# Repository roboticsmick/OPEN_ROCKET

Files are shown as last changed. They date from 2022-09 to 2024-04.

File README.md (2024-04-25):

# OPEN LOW COST ROCKET

An open designed low cost rocket build using 3D printed parts and a laser cutter. Design uses a Von Karman Nose Cone profile (optimum nose cone profile for rockets). Nosecone has space for a small payload bay. All parts should be printables without supports on Launchpad printers. You need to use the large Lulzbot due to height of nosecone. 29mm motor mount. A spacer is required for 24mm motor. Have successfully launched rocket using a E24 and G78 motor. 

Note: PLA deforms if left in the sun or it gets hot. Make sure to keep the nosecone out of the sun for extended periods of time. If it is in the sun, make sure the end caps are in to help reinforce the nosecone to prevent it deforming. 

#### Build 1:


#### Build 2:


## Parts list:
### Hardware to purchase:
1. 1 x PPS Mailing Tube 60 x 600 mm (Officeworks)
2. 3 x 12mm M3 countersunk hex bolts
3. 1 x M3 eyebolt - 10-15mm threaded bolt length (if the bolt length is longer and you have an avionics payload, make sure the bolt doesn't interfere with the avionics mounting in the nosecone)
4. 6 x M3 nuts
5. 2 x rail buttons (AusRocketry sell for $5)
6. 1 x parachute
7. 1 x nomex chute protector or wadding
8. 1 x shock cord - 2-3m long
9. 1 x epoxy
10. 2 x Sandpaper - 100 and 400 grit

### 3D printed parts:
1. 2 x Laser cutter jigs (holds the body tube straight and allows accurate 120 degree rotation of the body tube in the laser cutter when cutting out the fin slots).
2. 1 x Motor retainer (print with the thread at the top)
3. 1 x Motor tube (print with the thread at the top)
4. 1 x Nosecone plate / bulkhead
5. 1 x Nosecone (250mm length based on maximum Z Axis height of 3D printer).

### Plywood (4mm plywood):
3. 1 x laser shield (slots into laser cutter jig slot to prevent laser cutter from burning the opposing side of body tube when cutting fin slots)
4. 1 x Upper centring ring
5. 1 x Lower centring ring
6. 3 x Fins

## Steps:
### Body tube fin slots
1. Insert the laser cutter jigs into each end of the body tube. 
Rest the jigs on a flat surface and rotate and jiggle the tube until both jigs are sitting flat on the surface. Make sure they are still inserted into the tube. Add some masking tape to lock this position in place.
2. The jig has 3 centre markers for marking 3 equidistant marks on the tube to align laser cutter. 
3. Mark the tube at the marker points, then use a right angle ruler to draw lines along motor tube.
4. Measure up 66mm along the line and mark this point. This is where you will align the laser cutter centre point.
5. Insert the laser cutter shield into the slot parallel with the laser cutter bed. Rotate this piece of plywood after each cut. 
6. Make sure the laser cutter bed is correctly positioned and square in the lasercutter. Sometimes people bump it and it is not square. Insert the tube into laser cutter, and make sure the jig is aligned squarley with the lasercutter in one corner. The legs of the jig are square so it can be aligned against the lasercutter bed. It is important you place it in a repeatable position in the laser cutter, so that after the first cut of the fin slot, you can remove the jig, rotate it 120 degrees, then place it back into the same position. 




6. Centre the laser cutter on the mark made at the 66mm point and load in the fin slot template. You can position the laser cutter pointer to be in the centre of the object to be cut.
7. Cut the fin slot.
8. Remove the laser cutter shield, and rotate it to a new position that is parrallel to the next fin slot to cut.
9. Rotate the body tube, and reposition in the same location.
10. Recentre the laser cutter and repeat cut. 
11. Do this until all three fins are cut, remembering to move the laser cutter shield each time to prevent the laser cutter damaging the opposing wall.

### Fins and motor:
1. Glue upper ring to top of motor tube. Make sure it dries on a flat surface. Make sure not to get glue on fin guide slots or the holes to tie the parachute chord. 
2. Tie the parachute chord through the two holes in upper centering ring using a fishing knot.
3. Add epoxy fillet to upper ring and to the parachute chord to ensure strong bond and secure the chord. You can use a little masking tape after epoxying to keep the cord in the correct position to dry.
4. Place lower ring on motor tube and screw on motor retainer.
5. Test fit fins to ensure they fit cleanly into fin slots. Sand if needed.
6. Test fit motor tube into rocket body, noting were upper ring sits in motor tube.
7. Add glue to rocket body tube where the upper ring will sit.
8. Slide in motor tube to where glue sits. Align motor tube to fin slots and let dry.
9. Remove motor retainer cap and lower centering ring.
10. Add glue to guide slots and glue in fins. Motor tube has fin guides that will ensure fins are relatively straight. Leave to dry properly.
11. For added strength, add internal fillets to fins against body tube and motor tube.
12. Glue in lower centreing ring.
13. Use masking tape on outer tube to mask off where the outer fillets for the fins will go.
14. Add epoxy fillets for the fins.  Do this in 3 goes to allow time for the epoxy to settle when drying, before rotating to the next fin.
15. Remove the tape before epoxy sets fully and smooth epoxy againt body tube to minimise sanding when dry (otherwise there will be a little step the height of the masking tape).
16. Let epoxy set for 24 hours.





### Launch lugs / Rail buttons:
1. Drill holes into tube for rail buttons (1 into lower centring ring and 1 at centre of pressure (just below where the parachute sits in body tube to prevent it catching when it ejects)
2. Rough up where the rail buttons will mount on the body tube with sandpaper to allow a better grip for the epoxy.
3. Add epoxy into rail button holes, then screw in rail buttons. Clean up any excess epoxy with tissue.
4. For upper rail button, add extra epoxy to inner tube to ensure a more secure bond and prevent the thread sticking out and snagging the parachute (use a long piece of wood to get the epoxy into the tube and smooth it out so it creates a smooth blob around thread).

### Nosecone:
1. Clean out the nut mount inserts in the bulkhead to ensure there is no 3D filament stuck in the holes
2. Test fit the nuts to make sure they fit into points
3. Add small amount of epoxy to each of the nut mounts then press in the nuts (make sure no epoxy gets in the nut thread). You can use a nylon bolt to hold make sure the nuts are in place and no epoxy gets in the thread (just make sure to remove the bolt before the epoxy sets)
4. Screw in the eyebolt (add a little bit of epoxy when screwed in to prevent it from unwinding).
5. Attached shock cord and parachute to eyebolt.

#### Von Karman Nose Cone:


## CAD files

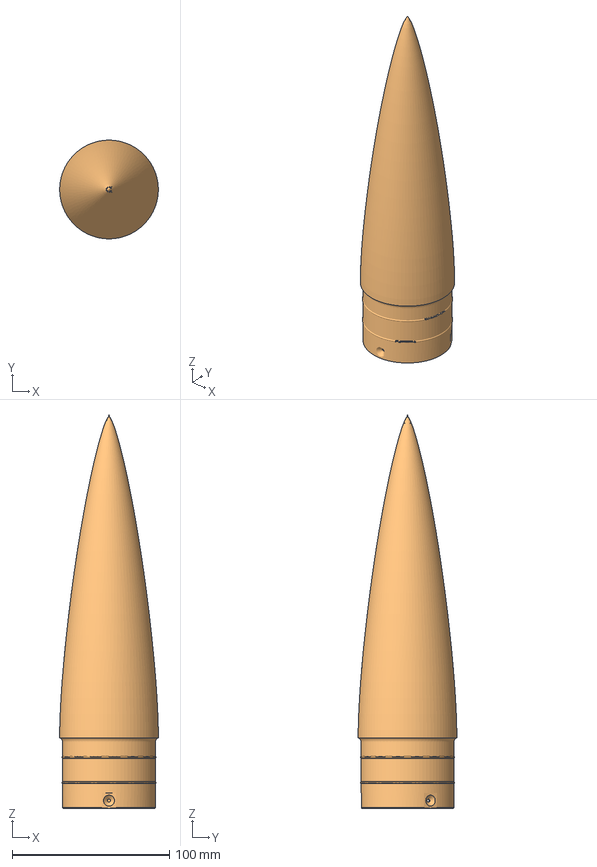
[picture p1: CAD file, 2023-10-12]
NOSECONE_VON_KARMAN.3mf
62.8 x 62.7 x 250.0 mm
Nose_Cone

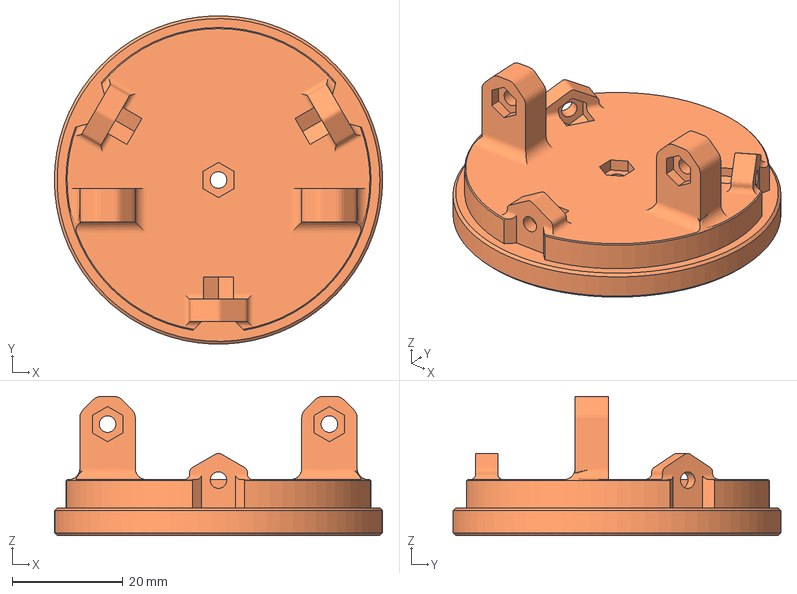
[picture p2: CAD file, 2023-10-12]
NOSECONE_PLATE.3mf
59.2 x 59.1 x 25.1 mm

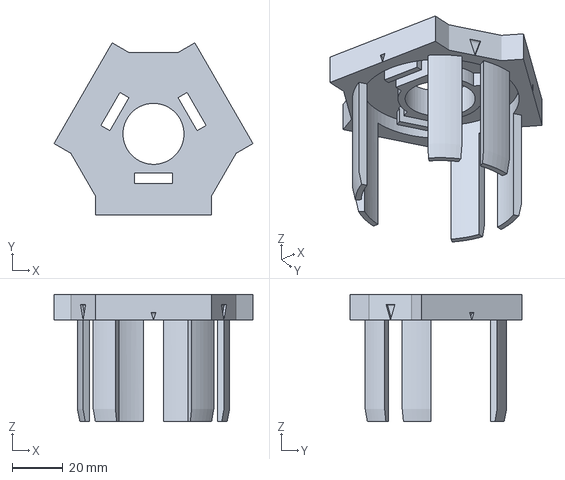
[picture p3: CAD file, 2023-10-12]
LASER_CUTTER_JIG.3mf
78.3 x 67.8 x 50.0 mm

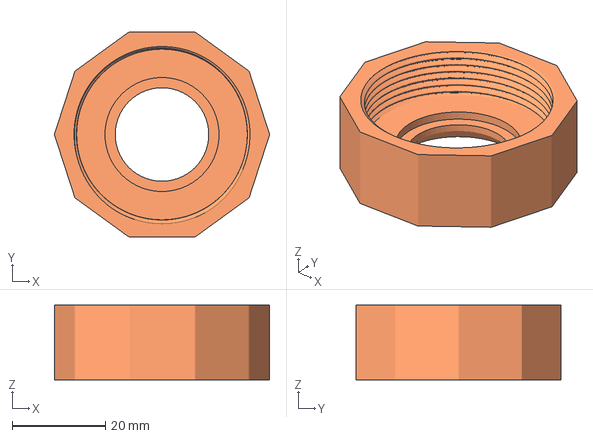
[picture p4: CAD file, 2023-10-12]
MOTOR_RETAINER.3mf
46.0 x 43.8 x 16.0 mm

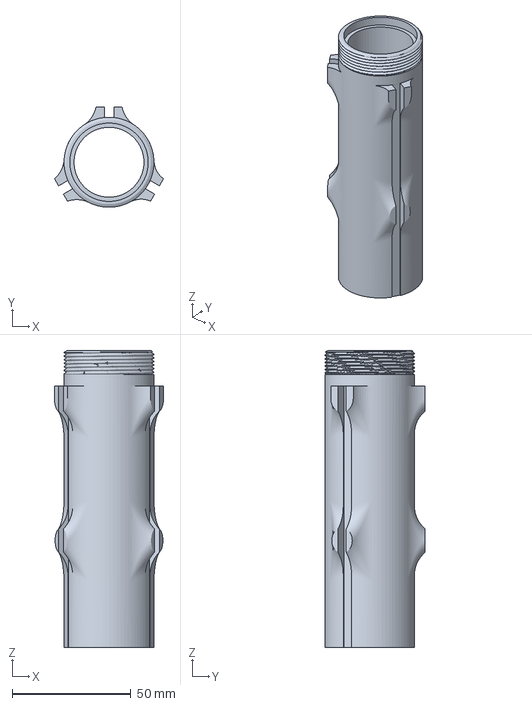
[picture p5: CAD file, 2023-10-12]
MOTOR_MOUNT.3mf
45.9 x 42.3 x 125.0 mm

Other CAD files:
FIN_BUILD_1.f3d
FIN_BUILD_2.f3d
LASER_CUTTER_JIG v8.f3d
MOTOR_RETAINER.f3d
NOSECONE_PLATE.f3d
NOSECONE_VON_KARMAN_FUSION360.f3d
SPACER_LOWER.f3d
SPACER_UPPER.f3d

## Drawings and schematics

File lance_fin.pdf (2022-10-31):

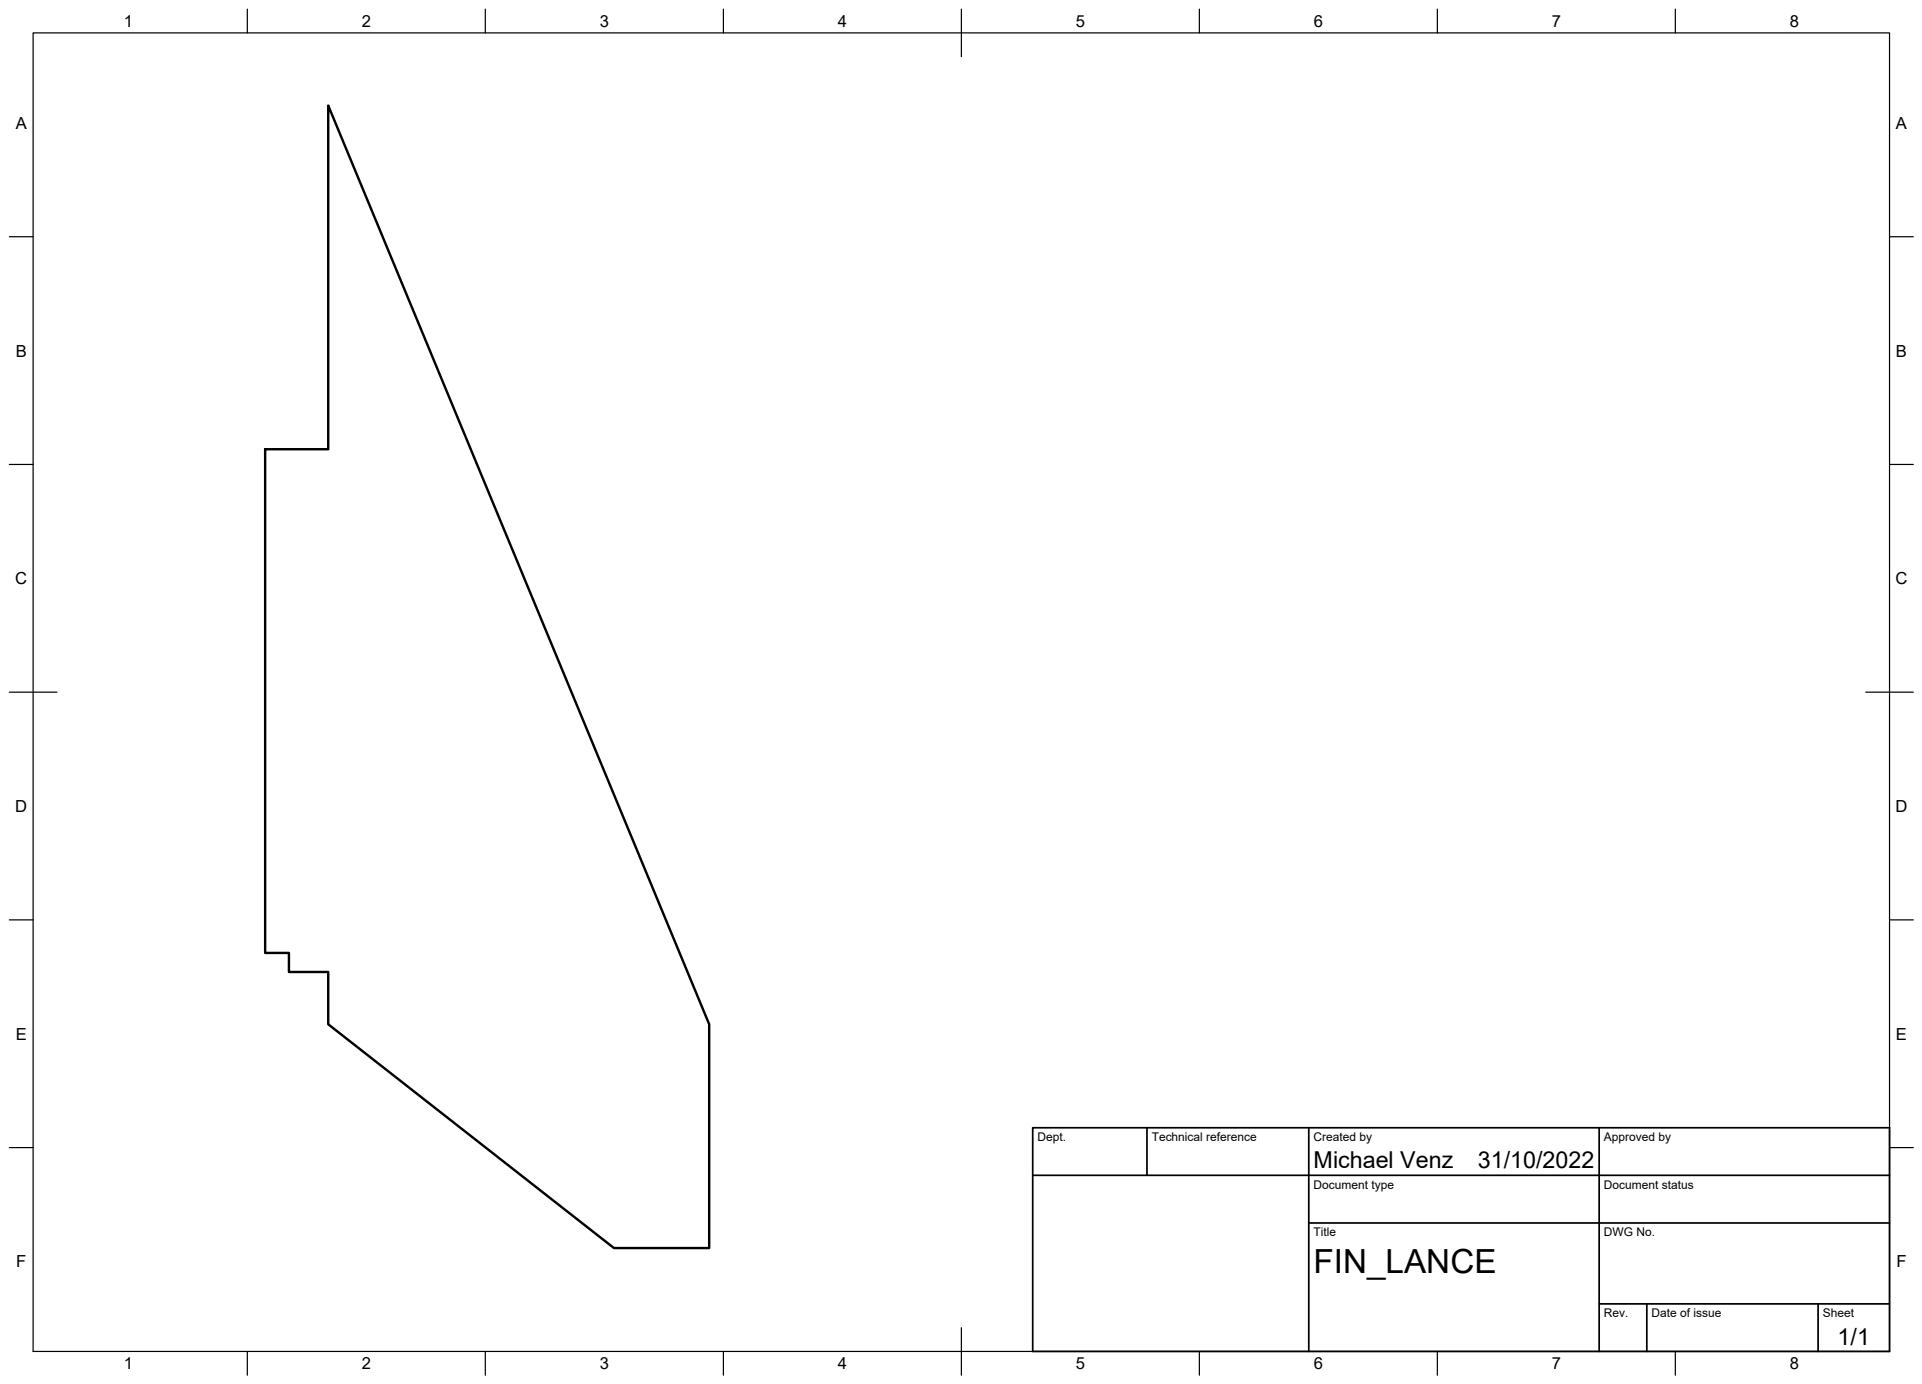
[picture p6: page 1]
Title; DWG No.; Rev.; Date of issue; Sheet

Dept. | Technical reference | Created by Michael Venz 31/10/2022 | Approved by

Document type | Document status

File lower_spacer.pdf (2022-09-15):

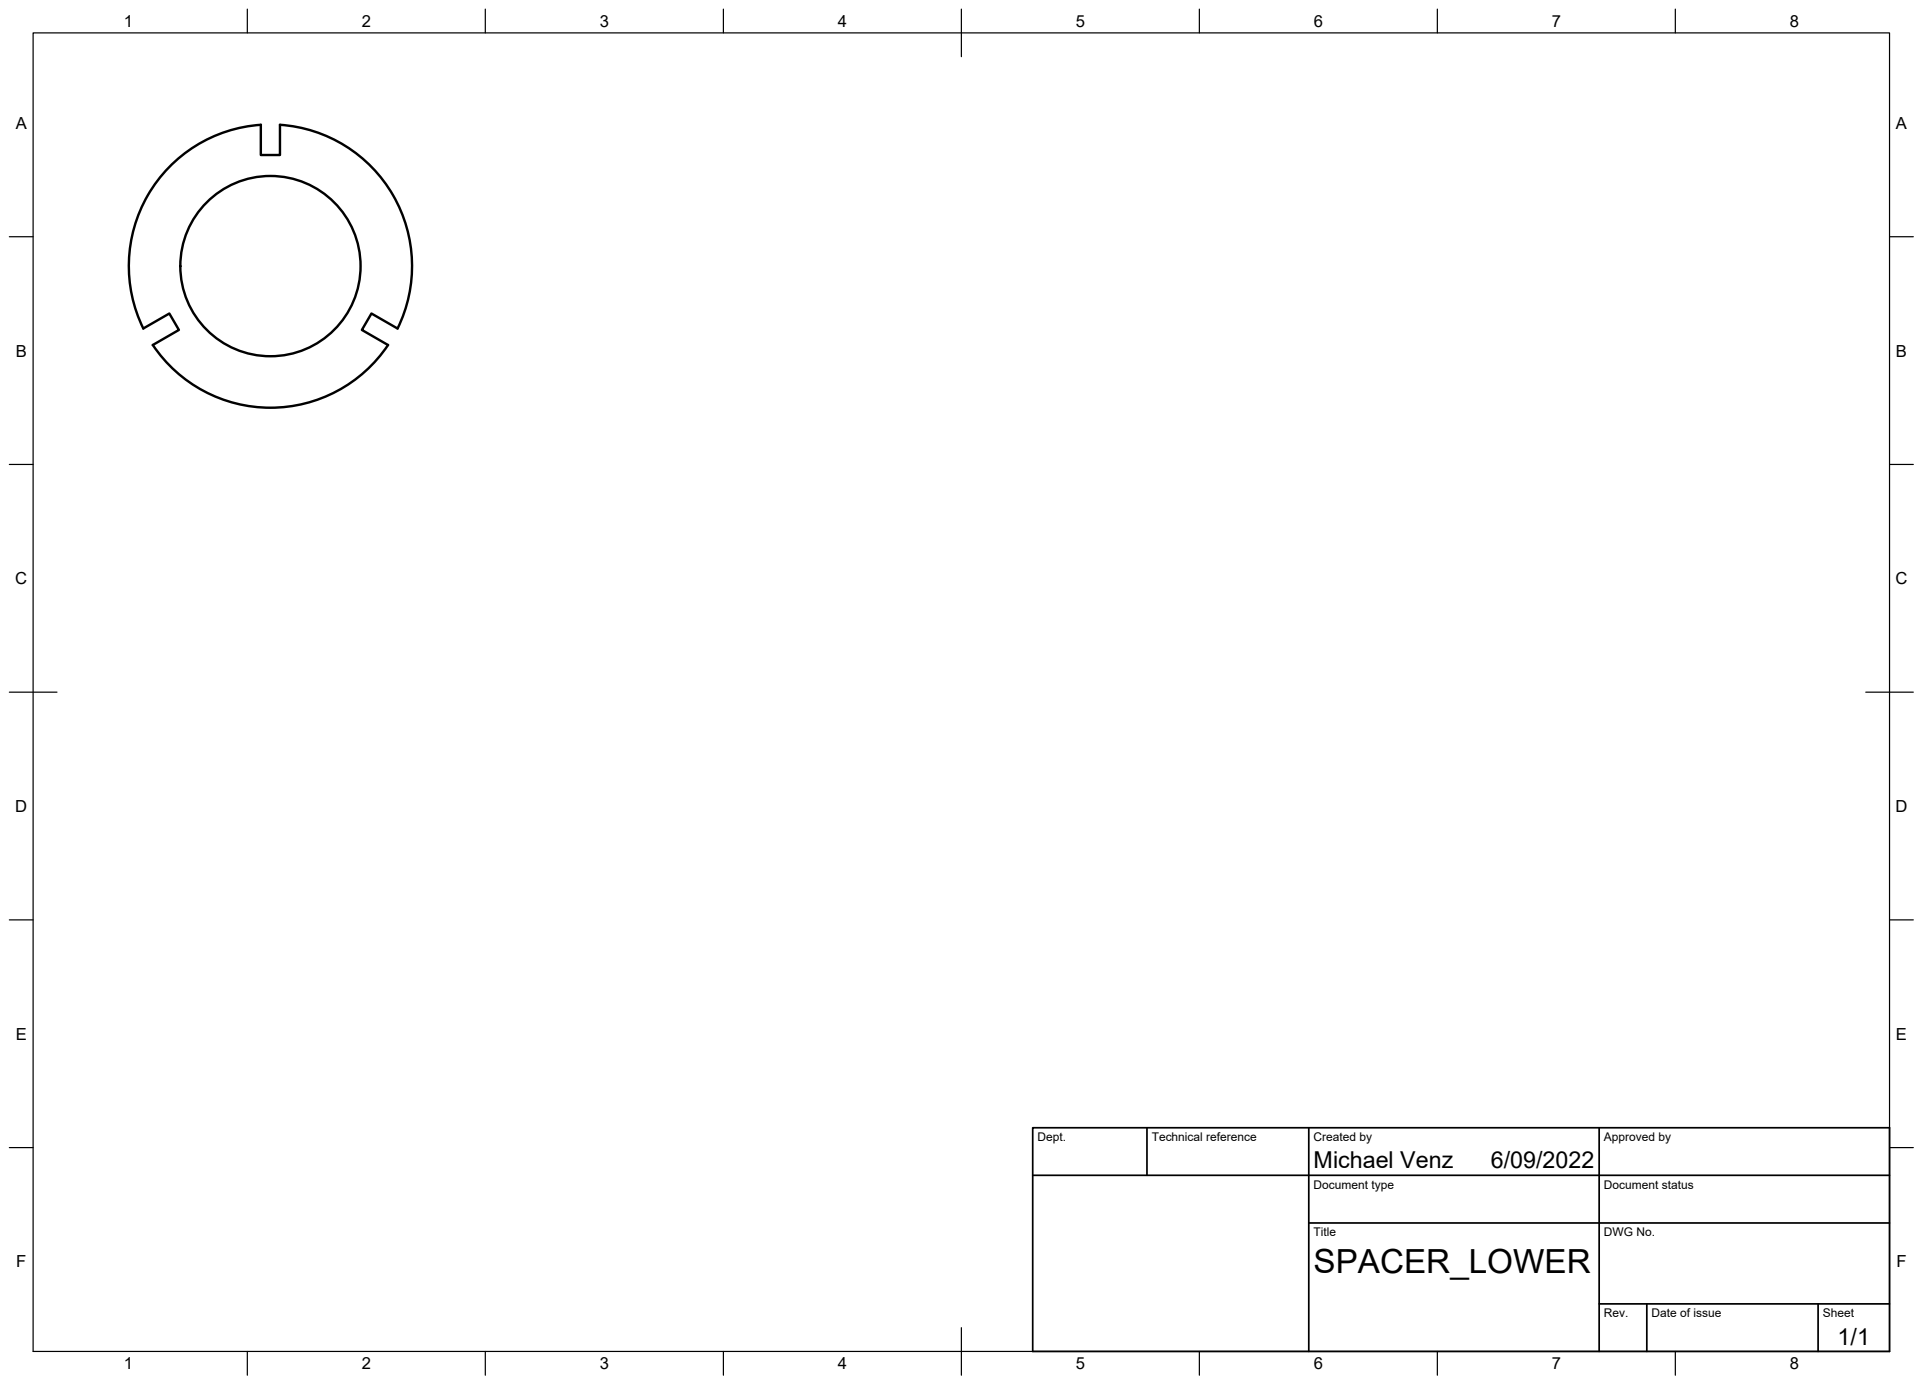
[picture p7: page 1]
Title; DWG No.; Rev.; Date of issue; Sheet

Dept. | Technical reference | Created by Michael Venz 6/09/2022 | Approved by

Document type | Document status
